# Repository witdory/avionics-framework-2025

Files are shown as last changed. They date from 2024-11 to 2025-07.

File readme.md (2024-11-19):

# Arduino rocket avionics firmware platform

This project provides a framework for Arduino to quickly build and maintain Rocket Avionics and can be expanded according to the user's intentions. Users can easily add various sensors they want to use to the Avionics system, set them to perform custom missions, and help manage mission performance by flight stage throughout the entire flight process. This is significant in that it provides an expandable avionics framework based on Arduino, which is easily accessible, instead of existing expensive avionics such as Pixhawk. In addition, it provides not only software but also hardware design that includes basic sensors needed for avionics, helping to produce a low-cost avionics system in a short time.

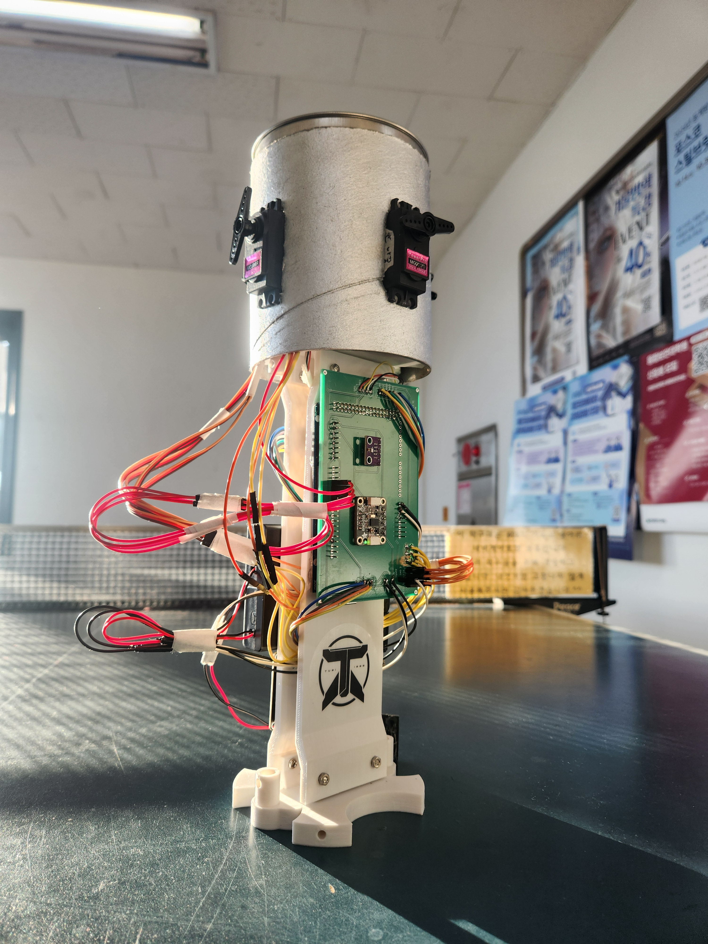
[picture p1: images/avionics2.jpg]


## feature
1. Quick and convenient sensor addition and management
2. Custom launch stages and mission control
3. Providing communication packets for efficient telemetry transmission and reception with ground stations
4. High reusability and maintainability
5. Provide hardware circuit design
6. support canard fin pid control

## software architecture
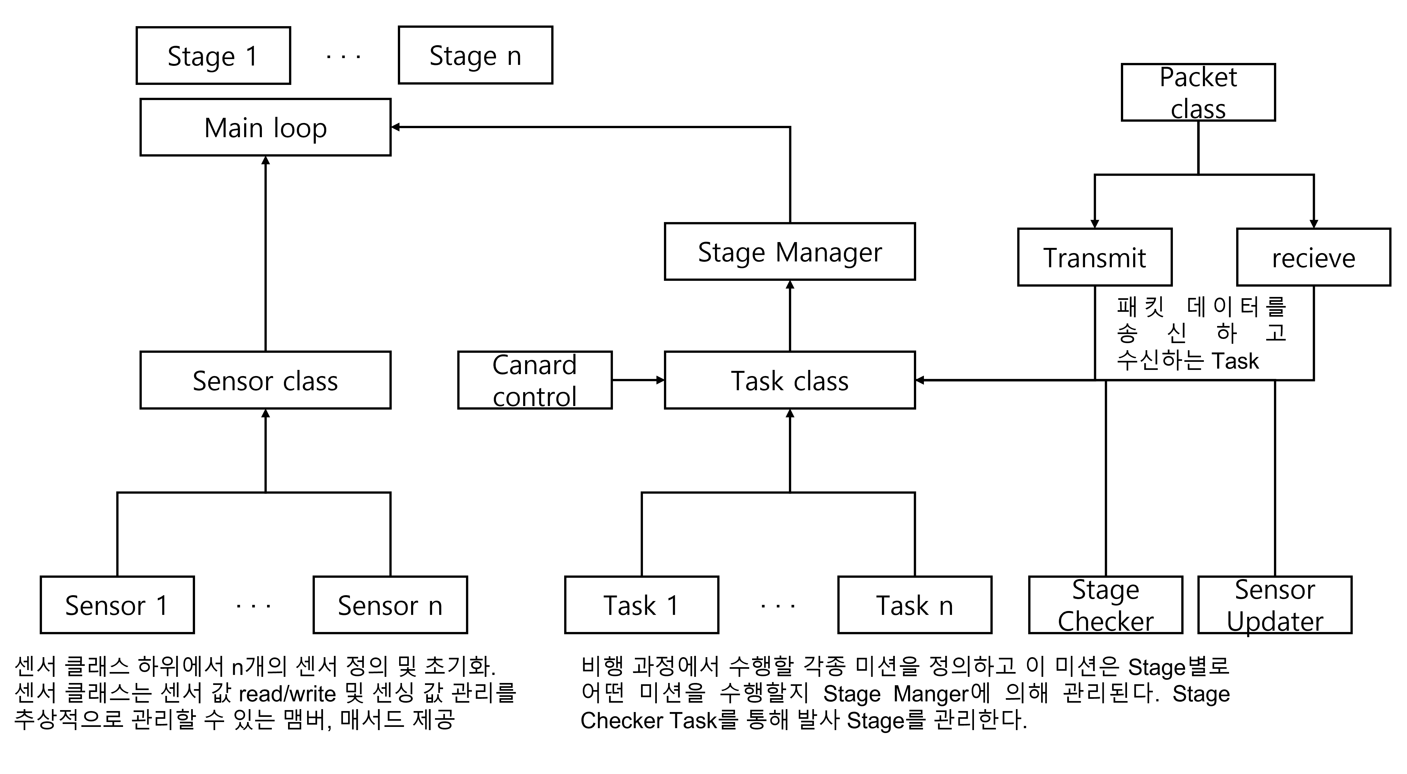
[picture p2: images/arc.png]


## packet architecture
In order to reduce unnecessary bit transmission during the communication process and ensure communication reliability and real-time, packets were designed and protocols were created.
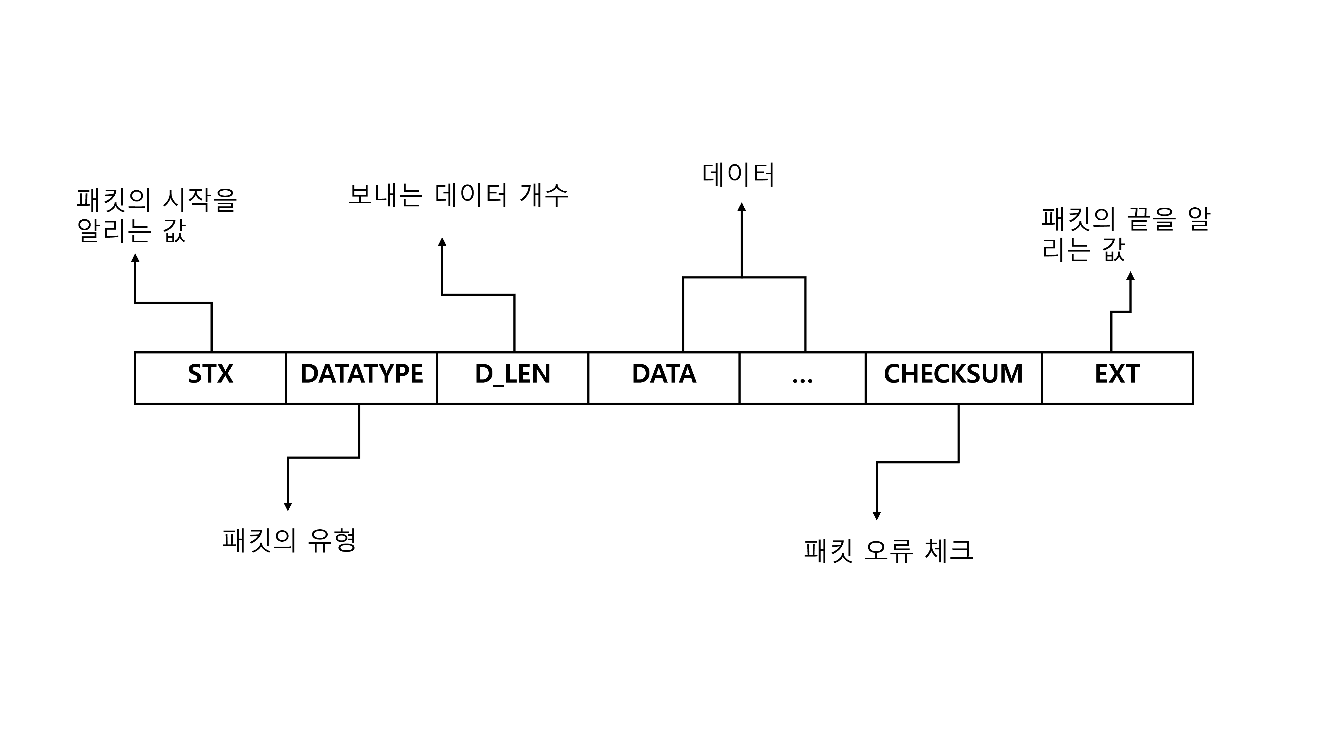
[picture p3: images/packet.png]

Data types are classified as follows. At this time, rocketstate, cmd, etc. must transmit and receive data accurately, so like the TCP protocol, when data is received from the receiver, it sends an ACK to the transmitter. If the ACK is not received from the transmitter, it is designed to transmit the data one more time. Like sensor telemetry, it sends an ACK to the transmitter. Data where real-time is important were excluded from this process.
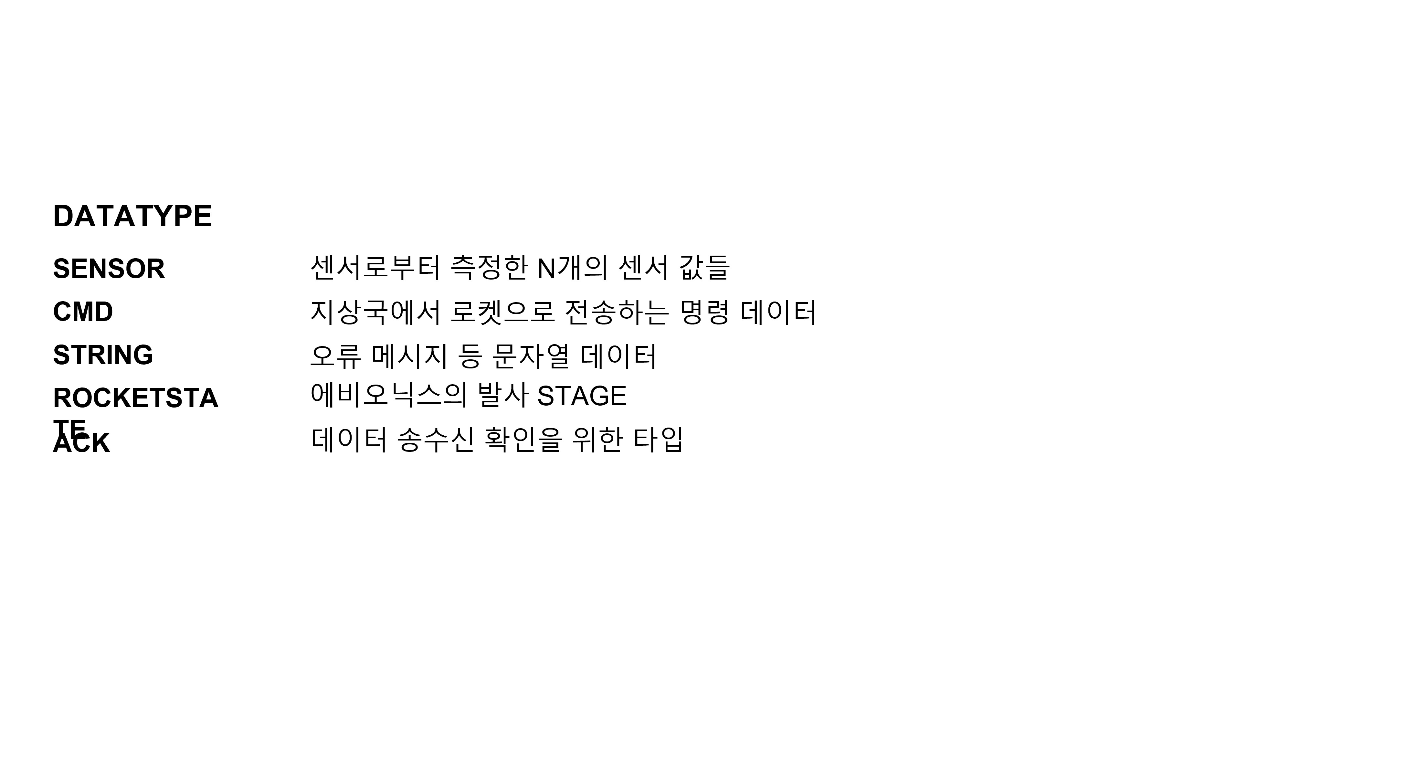
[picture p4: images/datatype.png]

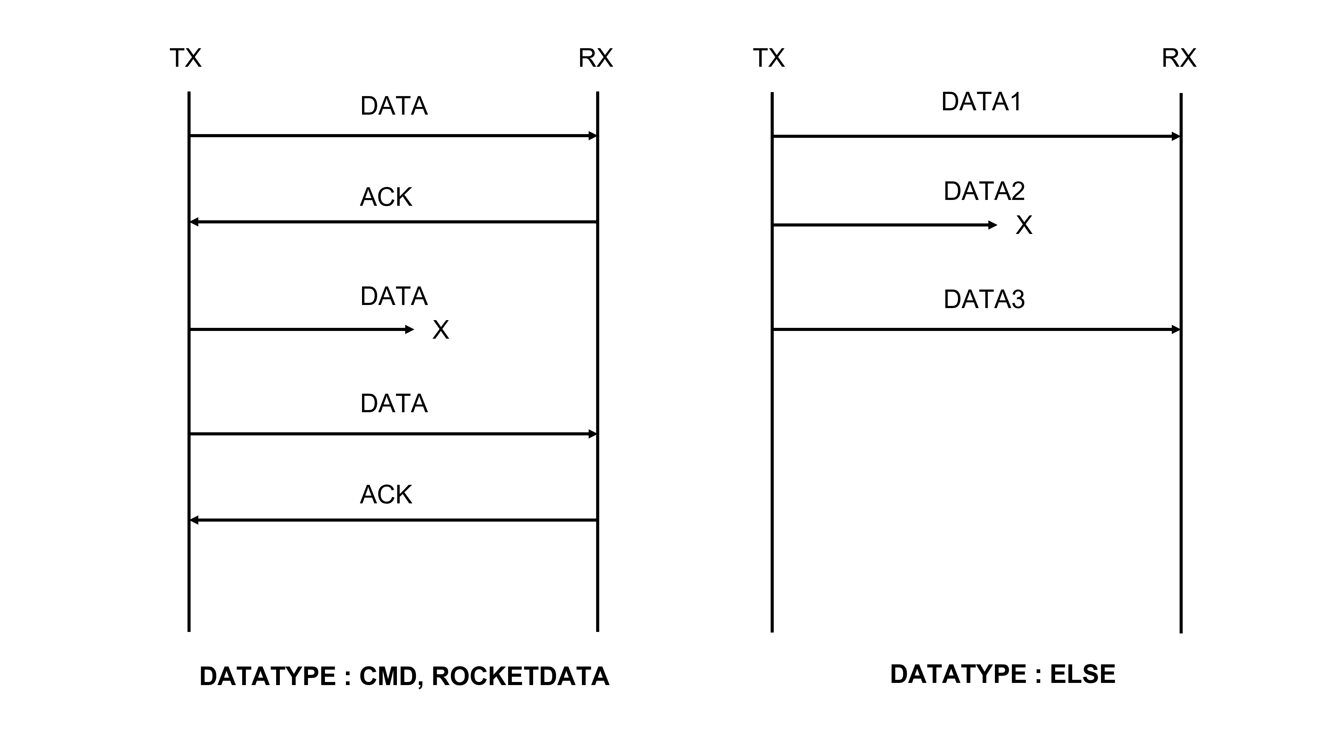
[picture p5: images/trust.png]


## uml
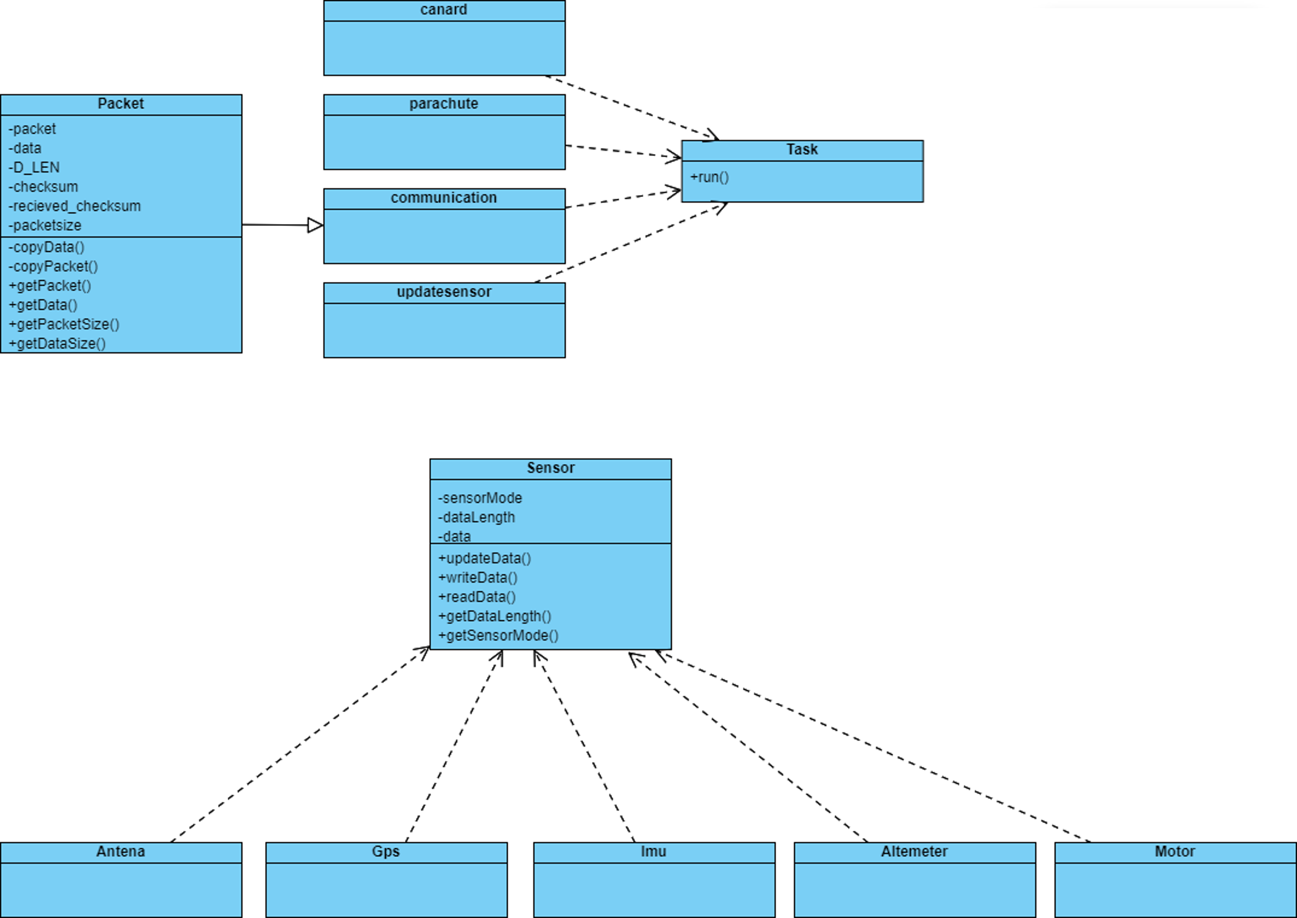
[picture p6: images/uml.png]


## hardware
The hardware basically consists of GPS, IMU, barometer, SD reader, motor, and communication module. In addition, the user can replace and add sensors as needed. The initial version of the hardware used a breadboard, and the latest version had a new PCB design to increase stability.
excluded from this process.
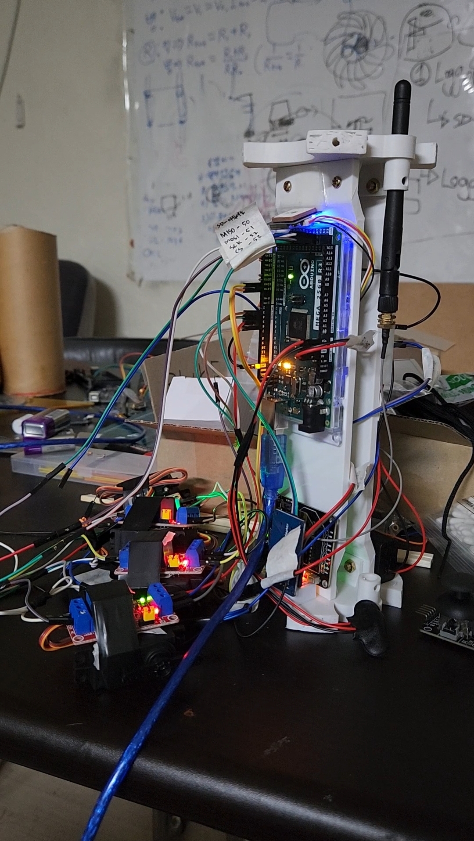
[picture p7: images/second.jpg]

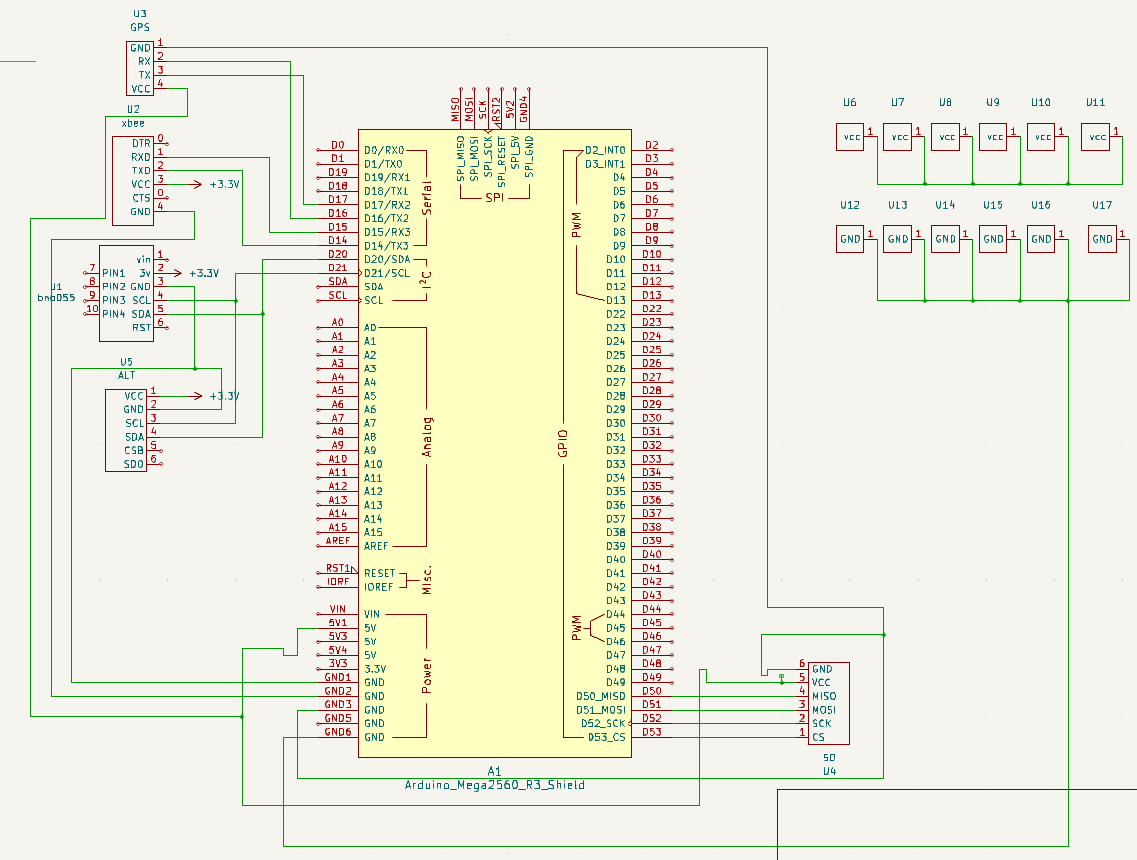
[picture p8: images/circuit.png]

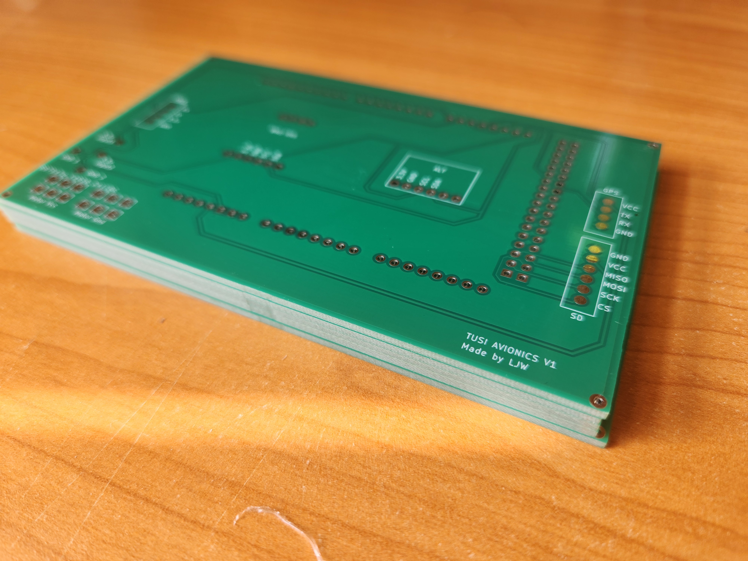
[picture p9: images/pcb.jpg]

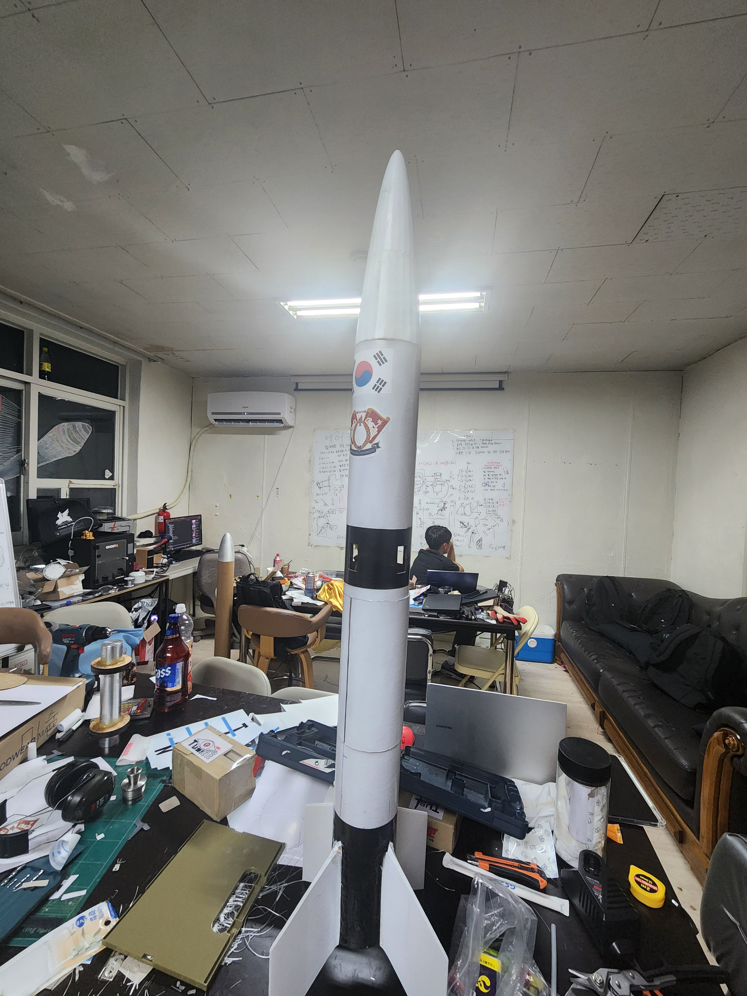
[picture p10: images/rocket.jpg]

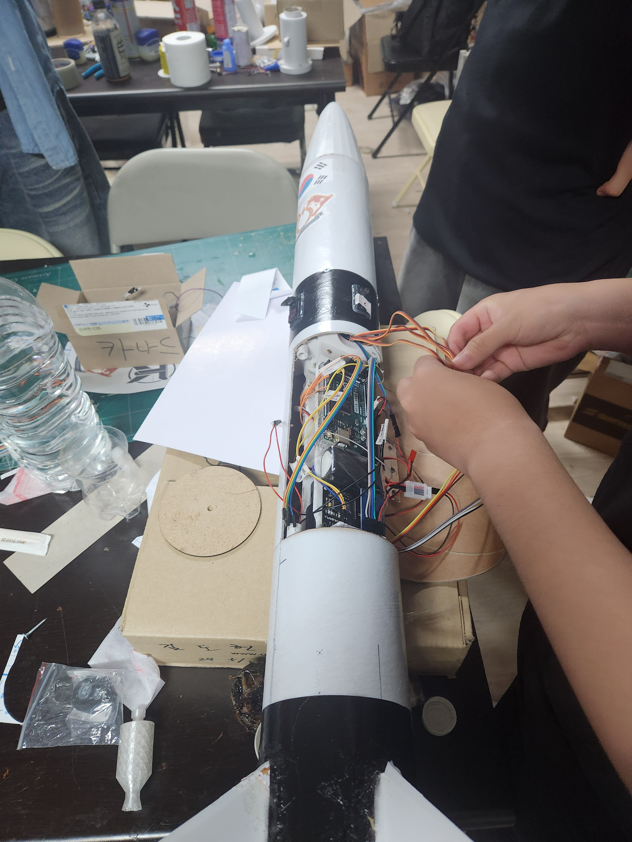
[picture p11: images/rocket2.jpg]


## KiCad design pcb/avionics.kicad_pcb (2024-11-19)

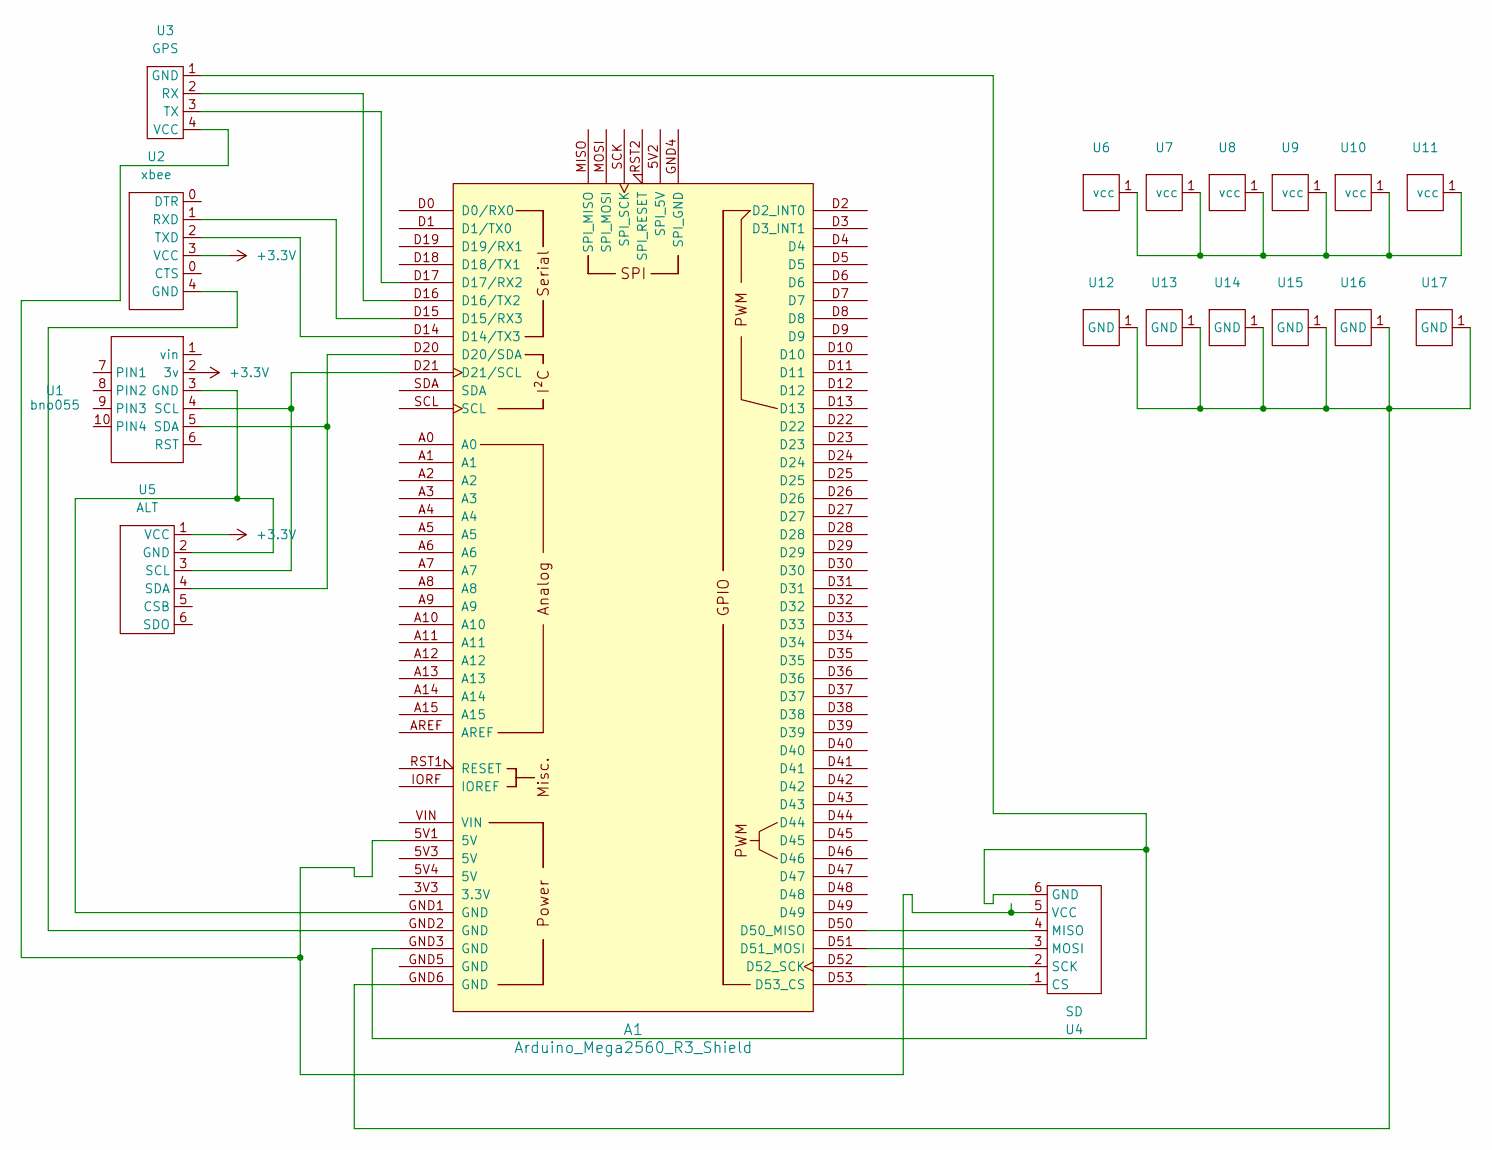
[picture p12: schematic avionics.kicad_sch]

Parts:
A1: Arduino_Mega2560_R3_Shield
U1: bno055
U2: xbee
U3: GPS; gps
U4: SD; sd
U5: ALT; bmp280
U6, U7, U8, U9, U10, U11: motor_vcc
U12, U13, U14, U15, U16, U17: motor_gnd

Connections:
+3.3V: U1.2 (3v), U2.3 (VCC), U5.1 (VCC)
unnamed: A1.D14 (D14/TX3), U2.2 (TXD)
unnamed: A1.D15 (D15/RX3), U2.1 (RXD)
unnamed: A1.D16 (D16/TX2), U3.2 (RX)
unnamed: A1.D17 (D17/RX2), U3.3 (TX)
unnamed: A1.D20 (D20/SDA), U1.5 (SDA), U5.4 (SDA)
unnamed: A1.D21 (D21/SCL), U1.4 (SCL), U5.3 (SCL)
unnamed: A1.D50 (D50_MISO), U4.4 (MISO)
unnamed: A1.D51 (D51_MOSI), U4.3 (MOSI)
unnamed: A1.D52 (D52_SCK), U4.2 (SCK)
unnamed: A1.D53 (D53_CS), U4.1 (CS)
unnamed: A1.GND1 (GND), U1.3 (GND), U5.2 (GND)
unnamed: A1.GND2 (GND), U2.4 (GND)
unnamed: A1.GND3 (GND), U3.1 (GND), U4.6 (GND)
unnamed: A1.5V1 (5V), U3.4 (VCC), U4.5 (VCC)
unnamed: U6.1 (vcc), U7.1 (vcc), U8.1 (vcc), U9.1 (vcc), U10.1 (vcc), U11.1 (vcc)
unnamed: A1.GND6 (GND), U12.1 (GND), U13.1 (GND), U14.1 (GND), U15.1 (GND), U16.1 (GND), U17.1 (GND)

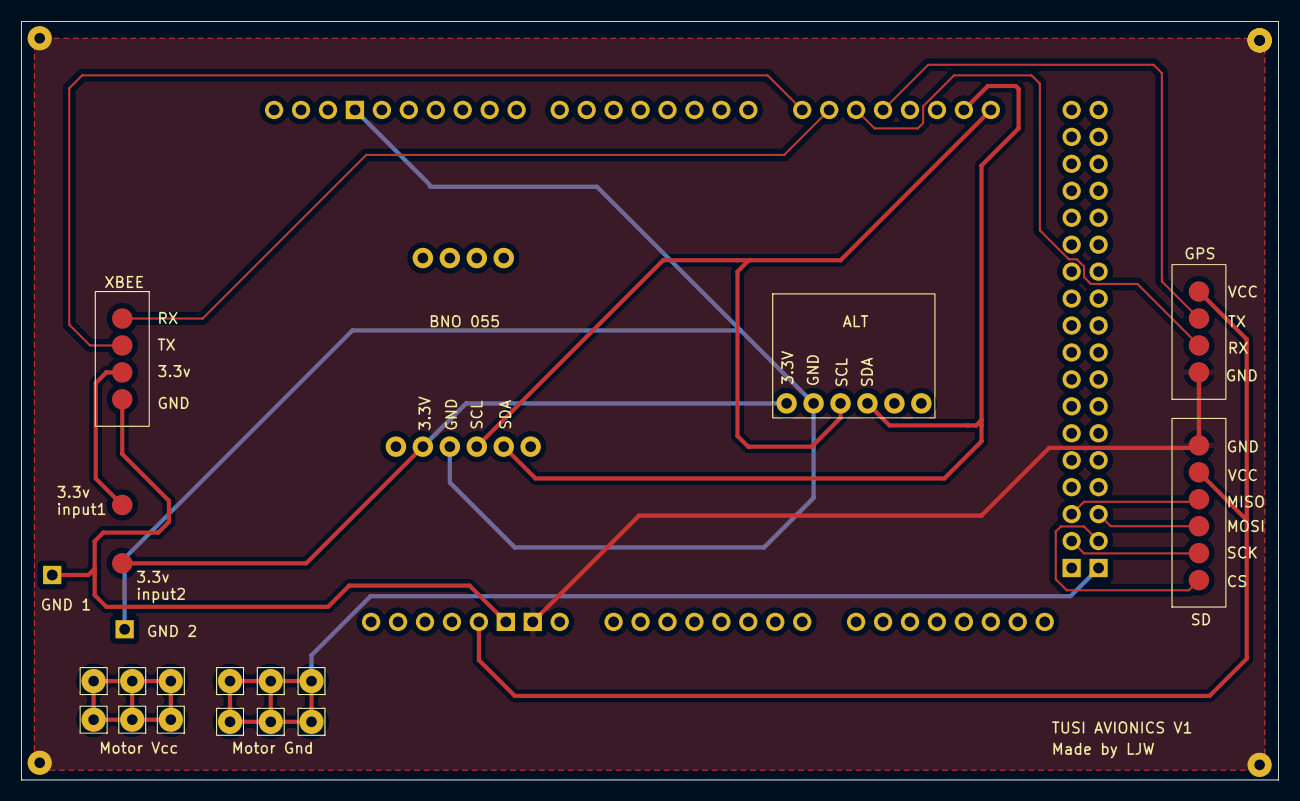
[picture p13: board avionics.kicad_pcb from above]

Board: 2 copper layers, 118.5 x 71.5 mm, 17 parts (0 on the bottom side), 17 nets.

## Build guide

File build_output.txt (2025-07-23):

Processing uno_r4_minima (platform: renesas-ra; board: uno_r4_minima; framework: arduino)
--------------------------------------------------------------------------------
Verbose mode can be enabled via `-v, --verbose` option
CONFIGURATION: https://docs.platformio.org/page/boards/renesas-ra/uno_r4_minima.html
PLATFORM: Renesas RA (1.7.0) > Arduino Uno R4 Minima
HARDWARE: RA4M1 48MHz, 32KB RAM, 256KB Flash
DEBUG: Current (cmsis-dap) External (cmsis-dap, jlink)
PACKAGES: 
 - framework-arduinorenesas-uno @ 1.4.1 
 - tool-dfuutil-arduino @ 1.11.0 
 - toolchain-gccarmnoneeabi @ 1.70201.0 (7.2.1)
LDF: Library Dependency Finder -> https://bit.ly/configure-pio-ldf
LDF Modes: Finder ~ chain, Compatibility ~ soft
Found 29 compatible libraries
Scanning dependencies...
Dependency Graph
|-- Servo @ 1.2.2
|-- Adafruit Unified Sensor @ 1.1.15
|-- Adafruit BNO055 @ 1.6.4
|-- Adafruit BusIO @ 1.17.2
|-- SPI
|-- Adafruit BMP280 Library @ 2.6.8
|-- SD @ 1.3.0
|-- ME310G1 @ 0.1.0+sha.9dcccfb
|-- Wire
Building in release mode
Compiling .pio\build\uno_r4_minima\src\lte\persistent_tcp.cpp.o
Compiling .pio\build\uno_r4_minima\src\main.cpp.o
Linking .pio\build\uno_r4_minima\firmware.elf
Checking size .pio\build\uno_r4_minima\firmware.elf
Advanced Memory Usage is available via "PlatformIO Home > Project Inspect"
RAM:   [===       ]  30.7% (used 10060 bytes from 32768 bytes)
Flash: [===       ]  34.9% (used 91456 bytes from 262144 bytes)
Building .pio\build\uno_r4_minima\firmware.bin
========================= [SUCCESS] Took 2.47 seconds =========================

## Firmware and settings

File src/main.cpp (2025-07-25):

#include "modules.h"
#include "task/transmit.h"
#include <SoftwareSerial.h>

// Pin definitions
#define MPU_RX 5
#define MPU_TX 6
#define BMP_CS 10
#define SD_CS 8
#define PARACHUTE_PIN 9

Modem modem;
HttpClient httpClient(&modem);
PersistentTCP tcp(&modem, "114.108.80.58", 10025);



ALTEMETER alt(READ_ONLY, 1, BMP_CS);
GPS gps(READ_ONLY, 2, modem.getModem());
IMU imu(READ_ONLY, 3);
MOTOR parachute_motor(WRITE_ONLY, 180, PARACHUTE_PIN);
LOGGER logger(SD_CS);
Stage stage;

bool sdDataSentApogee = false;

Parachute parachute(&parachute_motor);
Transmit transmit(&imu, &alt, &gps, &logger, &tcp);
UpdateSensor updatesensor(&imu, &alt, &gps);
StageChecker stagecheck(&imu, &alt, &gps, &stage,&logger);

// 이전 코드...



unsigned long initTime, currentTime; 

inline void getCommand(String command){
    // Serial.print("getCommand called with: ");
    // Serial.println(command);
    if (command == "Ready") {
        stage = READY;
        Serial.println("Stage changed to: READY (from Ready command)");
        String stageStr = "READY";
        // httpClient.post(SERVER, 8000, "/state", stageStr.c_str());
    } else if (command == "Injection") {
        //parachute.run();
        stage = APOGEE;
        Serial.println("Stage changed to: APOGEE (from Injection command)");
        String stageStr = "APOGEE";
        // httpClient.post(SERVER, 8000, "/state", stageStr.c_str());
    } else if (command == "StageChange") {
        switch (stage)
        {
        case INIT: {
            stage = CALIBRATION;
            Serial.println("Stage changed to: CALIBRATION (from StageChange command, was INIT)");
            // String stageStrInit = "READY";
            // httpClient.post(SERVER, 8000, "/state", stageStrInit.c_str());
            break;
        }
        case CALIBRATION: {
            stage = READY;
            Serial.println("Stage changed to: READY (from StageChange command, was CALIBRATION)");
            // String stageStrInit = "READY";
            // httpClient.post(SERVER, 8000, "/state", stageStrInit.c_str());
            break;
        }
        case READY: {
            stage = ASCENDING;
            Serial.println("Stage changed to: ASCENDING (from StageChange command, was READY)");
            stagecheck.setAscendingTime(millis());
            // String stageStrReady = "ASCENDING";
            // httpClient.post(SERVER, 8000, "/state", stageStrReady.c_str());
            break;
        }
        case ASCENDING: {
            stage = APOGEE;
            Serial.println("Stage changed to: APOGEE (from StageChange command, was ASCENDING)");
            String stageStrAscending = "APOGEE";
            // httpClient.post(SERVER, 8000, "/state", stageStrAscending.c_str());
            break;
        }
        case APOGEE: {
            stage = DESCENDING;
            Serial.println("Stage changed to: DESCENDING (from StageChange command, was APOGEE)");
            String stageStrApogee = "DESCENDING";
            // httpClient.post(SERVER, 8000, "/state", stageStrApogee.c_str());
            break;
        }
        default: {
            break;
        }}
    }
}

void setup(){
    //초기 시간 저장
    initTime = millis();
    // 초기 stage INIT으로 초기화
    stage = INIT;
    // Serial.println("Stage changed to: INIT");
    pinMode(10, OUTPUT); // BMP280 CS
    pinMode(8, OUTPUT);  // SD카드 CS
    digitalWrite(10, HIGH); // BMP280 비활성화
    digitalWrite(8, HIGH);  // SD카드 비활성화

    // 센서들 연결 및 초기화
    Serial.begin(115200);
    
    Serial.println("INIT");
    gps.init(); // GPS init is always called
    Serial.println("GPS DONE");
    imu.init();
    Serial.println("IMU DONE");
    digitalWrite(10, HIGH); // BMP280 CS 비활성화
    // logger.init();
    Serial.println("SD DONE");
    digitalWrite(8, HIGH); // SD카드 CS 비활성화
    alt.init();
    Serial.println("ALT DONE");
    
    // parachute_motor.init2();
    Serial.println("MOTOR");

    if(modem.init(APN)){
        Serial.println("LTE DONE");
    } else {
        Serial.println("LTE FAILED");
    }

    Serial.println("Attempting TCP connect...");
    if (tcp.connect()) {
        Serial.println("TCP 연결 성공!");
        // TCP 연결 성공 후 초기 상태를 서버로 HTTP POST 전송 (포트 8000)
        String stageStr = "INIT";
        // httpClient.post(SERVER, 8000, "/state", stageStr.c_str());
        // TCP 연결 성공 후 초기 상태를 PersistentTCP (포트 10025)로 전송
        Serial.println("Sending INIT_STATE:INIT...");
        if (tcp.send("INIT_STATE:INIT")) {
            Serial.println("INIT_STATE:INIT sent successfully.");
        } else {
            Serial.println("INIT_STATE:INIT send failed.");
        }
    } else {
        Serial.println("TCP 연결 실패");
    }

    // 지상국으로 초기화 완료 되었다고 데이터 전송
    Serial.println("INIT");
    // delay(100);
    Serial.println("Stage, INIT");
    String log = "INIT\n";
    // logger.writeData(log);
    digitalWrite(13, LOW);
}

void loop(){
    Serial.print("Stage: ");
    Serial.println(stage);
    
    String command; // Declare command here for broader scope

    if(stage == INIT){
        updatesensor.run(stage);

        // 1. TCP 연결 확인 및 재연결
        if (!tcp.isConnected()) {
            Serial.println("TCP not connected. Attempting to reconnect...");
            if (!tcp.connect()) {
                Serial.println("TCP reconnection failed. Skipping loop.");
                delay(5000);
                return;
            }
            Serial.println("TCP reconnected successfully.");
        }

        // 2. 서버에 명령 요청
        tcp.send("COMMAND_REQUEST:STAGE:INIT");
        
        // 3. 서버로부터 응답 수신
        String raw_response = "";
        unsigned long receiveStartTime = millis();
        while (millis() - receiveStartTime < 5000) { // 5초 타임아웃
            raw_response = tcp.receive();
            if (raw_response.length() > 0) {
                break;
            }
            delay(100);
        }
        
        // 4. 수신된 데이터에서 실제 명령어 파싱
        String parsed_command = "";
        if (raw_response.indexOf("StageChange") != -1) {
            parsed_command = "StageChange";
        } else if (raw_response.indexOf("Ready") != -1) {
            parsed_command = "Ready";
        } else if (raw_response.indexOf("Injection") != -1) {
            parsed_command = "Injection";
        } else if (raw_response.indexOf("OK") != -1) {
            parsed_command = "OK";
        }
        
        Serial.print("Parsed command: '"); Serial.print(parsed_command); Serial.println("'");

        // 5. 파싱된 명령어로 로직 처리
        if (parsed_command.length() > 0) {
            if (parsed_command != "OK") {
                getCommand(parsed_command);
            } else {
                Serial.println("Received OK ack, holding stage.");
            }
        } else {
            Serial.println("No valid command keyword found in response.");
        }
    }
    else if(stage == CALIBRATION){
        updatesensor.run(stage);

        // 1. TCP 연결 확인 및 재연결
        if (!tcp.isConnected()) {
            Serial.println("TCP not connected. Attempting to reconnect...");
            if (!tcp.connect()) {
                Serial.println("TCP reconnection failed. Skipping loop.");
                delay(5000);
                return;
            }
            Serial.println("TCP reconnected successfully.");
        }

        // 2. 서버에 명령 요청
        tcp.send("COMMAND_REQUEST:STAGE:CALIBRATION");
        
        // 3. 서버로부터 응답 수신
        String raw_response = "";
        unsigned long receiveStartTime = millis();
        while (millis() - receiveStartTime < 5000) { // 5초 타임아웃
            raw_response = tcp.receive();
            if (raw_response.length() > 0) {
                break;
            }
            delay(100);
        }
        
        // 4. 수신된 데이터에서 실제 명령어 파싱
        String parsed_command = "";
        if (raw_response.indexOf("StageChange") != -1) {
            parsed_command = "StageChange";
        } else if (raw_response.indexOf("Ready") != -1) {
            parsed_command = "Ready";
        } else if (raw_response.indexOf("Injection") != -1) {
            parsed_command = "Injection";
        } else if (raw_response.indexOf("OK") != -1) {
            parsed_command = "OK";
        }
        
        Serial.print("Parsed command: '"); Serial.print(parsed_command); Serial.println("'");

        // 5. 파싱된 명령어로 로직 처리
        if (parsed_command.length() > 0) {
            if (parsed_command != "OK") {
                getCommand(parsed_command);
            } else {
                Serial.println("Received OK ack, holding stage.");
            }
        } else {
            Serial.println("No valid command keyword found in response.");
        }
    }
    else if(stage == READY){
        // Serial.println("Entering READY stage block.");
        // 텔레메트리 값 읽어오기 시작
        updatesensor.run(stage);

        // Serial.print("Altemeter: ");
        // Serial.println(alt._data[0]);

        // 읽은 텔레메트리 값 전송 및 저장
        // transmit.sendSensorData(stage); // Call directly

        // 만약 가속도 값이 크게 변화하면 상태 ASCENDING으로 바꿈 및 상태 변경 패킷 전송 및 저장
        stagecheck.run();
        // stage = ASCENDING;
        if (stage == ASCENDING){
            Serial.println("ASCENDING TRANSMIT");
            Serial.print("TCP Connected: "); Serial.println(tcp.isConnected() ? "true" : "false");
            if (!tcp.isConnected()) {
                Serial.println("TCP not connected. Attempting to reconnect...");
                if (!tcp.connect()) {
                    Serial.println("TCP reconnection failed. Skipping send/receive.");
                    delay(5000); // Wait before next attempt
                    return; // Skip current loop iteration
                }
                Serial.println("TCP reconnected successfully.");
            }
            if (tcp.send("COMMAND_REQUEST:STAGE:ASCENDING")) {
                Serial.println("ASCENDING TRANSMITTED successfully.");
            } else {
                Serial.println("ASCENDING TRANSMITTED failed.");
            }
        }
    }
    else if(stage == ASCENDING){
        Serial.println("Entering ASCENDING stage block.");
        // 텔레메트리 값 읽기 시작
        updatesensor.run(stage);
        // 텔레메트리 값 전송 및 저장
        
        // 읽은 텔레메트리 값 전송 및 저장
        Serial.print("TCP Connected: "); Serial.println(tcp.isConnected() ? "true" : "false");
        if (!tcp.isConnected()) {
            Serial.println("TCP not connected. Attempting to reconnect...");
            if (!tcp.connect()) {
                Serial.println("TCP reconnection failed. Skipping send/receive.");
                delay(5000); // Wait before next attempt
                return; // Skip current loop iteration
            }
            Serial.println("TCP reconnected successfully.");
        }
        transmit.sendSensorData(stage); // Call directly
        Serial.println("ASCENDING");
        stagecheck.run();
        
    }
    else if(stage == APOGEE){
        Serial.println("Entering APOGEE stage block.");
        // 텔레메트리 값 읽기 시작
        updatesensor.run(stage);
        // 낙하산 사출
        parachute.run();
        // delay(100);
        // APOGEE 진입 시 SD 카드 데이터 전송 (한 번만 실행)
        if (!sdDataSentApogee) {
            Serial.println("상승 데이터 전송");
            // transmit.sendSdCardDataToServer();
            sdDataSentApogee = true;
            stage = DESCENDING;
            stagecheck.setDescendingStartTime(millis()); // Initialize descendingStartTime here
        }
        transmit.sendSensorData(stage); // Call directly

        // stagecheck.run();

        
    }
    else if(stage == DESCENDING){
        // Serial.println("Entering DESCENDING stage block.");
        // 텔레메트리 값 읽기 시작
        updatesensor.run(stage);
        // 텔레메트리 값 전송 및 저장
        Serial.print("TCP Connected: "); Serial.println(tcp.isConnected() ? "true" : "false");
        if (!tcp.isConnected()) {
            Serial.println("TCP not connected. Attempting to reconnect...");
            if (!tcp.connect()) {
                Serial.println("TCP reconnection failed. Skipping send/receive.");
                delay(5000); // Wait before next attempt
                return; // Skip current loop iteration
            }
            Serial.println("TCP reconnected successfully.");
        }
        transmit.sendSensorData(stage); // Call directly
        stagecheck.run();
    }
    else if(stage == RETRIEVAL){
        // 이 스테이지에 처음 진입했을 때만 초기화를 실행하기 위한 static 변수
        static bool retrieval_initialized = false;

        // 초기화가 아직 안 됐다면 GPS 전원을 켠다.
        if (!retrieval_initialized) {
            Serial.println("--- Initializing RETRIEVAL Stage ---");
            Serial.println("Powering ON GNSS controller (will stay on)...");
            gps.getModem()->gnss_controller_power_management(1);
            retrieval_initialized = true; // 초기화 완료 플래그 설정
            delay(1000); // 모듈 전원이 켜질 때까지 잠시 대기
        }

        Serial.println("--- RETRIEVAL Cycle Start ---");

        // 1. GPS 데이터 수신 시도
        String gpsFixData = "";
        bool gpsSuccess = false;

        Serial.println("Attempting to get GPS fix...");
        me310::ME310::return_t rc_gps = gps.getModem()->gps_get_acquired_position();
        
        if (rc_gps == me310::ME310::RETURN_VALID) {
            String raw_data = (String)gps.getModem()->buffer_cstr(1);
            int colon_index = raw_data.indexOf(':');
            // 콜론(:) 뒤에 좌표 데이터가 있는지 확인
            if (colon_index != -1 && raw_data.charAt(colon_index + 1) != ',') {
                Serial.print("GPS Fix Acquired: ");
                Serial.println(raw_data);
                gpsFixData = raw_data;
                gpsSuccess = true;
            }
        }

        // 2. 수신 성공 시에만 10진수 좌표로 변환하고 서버로 전송
        if (gpsSuccess) {
            float latitude, longitude;
            if (gps.parseLatLng(gpsFixData.c_str(), latitude, longitude)) {
                
                Serial.print("==> Converted to Decimal Degrees: ");
                Serial.print(latitude, 6);
                Serial.print(", ");
                Serial.println(longitude, 6);

                String payload = "GPS_DATA:" + String(latitude, 6) + "," + String(longitude, 6);

                if (!tcp.isConnected()) {
                    Serial.println("TCP not connected. Reconnecting...");
                    tcp.connect();
                }
                
                if (tcp.isConnected()) {
                    Serial.print("Sending to server: ");
                    Serial.println(payload);
                    if (tcp.send(payload.c_str())) {
                        Serial.println("GPS data sent successfully.");
                    } else {
                        Serial.println("GPS data send failed.");
                    }
                } else {
                    Serial.println("Cannot send GPS data, TCP connection failed.");
                }

            } else {
                Serial.println("Failed to parse the acquired GPS data string.");
            }
        } else {
            Serial.println("No GPS fix yet. Will try again in the next cycle.");
        }
        
        // 3. 다음 위치 보고까지 대기 (GPS는 계속 켜져 있음)
        Serial.println("Waiting 30 seconds for next retrieval cycle...");
        delay(5000); 
    }
    delay(10);
}

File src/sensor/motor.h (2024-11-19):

#pragma once
#include <Servo.h>
#include "../lib/sensor.h"
#include <Arduino.h>
//서보모터는 pwm 핀에 연결해야한다. -> 3, 5, 6, 9, 10, 11

class MOTOR : public Sensor<bool> {
public:
    MOTOR(int8_t sensorMode, int16_t maxAngle, int pin)
        : Sensor<bool>(sensorMode), _maxAngle(maxAngle), _pin(pin) {}

    void init() { //setup() 함수의 기능
        ms.attach(_pin);
        setToZero();
    }

    void init2(){
        ms.attach(_pin);
    }

    void setToZero() {
        _currentAngle = 90;
        ms.write(_currentAngle);
    }

    void rotateToAngle(int number) { //loop() 함수의 기능
        _currentAngle = number;
        if (_currentAngle < -_maxAngle) {
            // 각도가 허용 범위를 벗어났을 경우 오류 처리
            _currentAngle = -_maxAngle;
        }
        else if (_currentAngle > _maxAngle) {
            _currentAngle = _maxAngle;
        }
        ms.write(_currentAngle+90);
    }

private:
    Servo ms;
    int16_t _currentAngle;
    int16_t _maxAngle;
    int16_t _pin;
};

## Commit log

2024-11-19 first commit
    [avionics.kicad_pcb, avionics.kicad_sch]
2025-07-22 feat: http 통신 기능 추가 및 retrieval stage 추가
2025-07-23 get_command 메소드 수정
2025-07-23 feat: persistent tcp 통신 적용
2025-07-23 feat: Stage 변경 기능 적용
2025-07-24 feat: stage 전환 적용
2025-07-24 fix: bmp280 오류 해결
    [altemeter.h, imu.h, main.cpp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]
2025-07-24 feat: Ascending, Apogee 감지 적용
2025-07-25 feat: Retrieval 감지 적용용
2025-07-25 feat: gps 정보 수신
2025-07-25 fix: gps 데이터 파싱 문제 해결
